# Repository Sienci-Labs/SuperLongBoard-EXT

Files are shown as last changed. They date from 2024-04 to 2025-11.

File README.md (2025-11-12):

# SuperLongBoard-EXT PCB Design
Hardware repo for the SLB-EXT board for the AltMill. These are all the raw build files that we're making available to the public so you can see and access the work that's been put in to make the SuperLongBoard-EXT as it currently exists. If you'd like to make it yourself, modify it, or suggest improvements feel free. Please note and respect the license we've chosen to distribute it under.

# License

This code has been created within the context of Open Hardware and is licensed under the "CERN-OHL-S v2". Please read more about this in the LICENSE file. You could redistribute and modify this source and make products using it under the terms of the CERN-OHL-S v2. This means stuff like licensing your changes reciprocally, giving attribution to us, and releasing hardware that this code runs on as CERN-OHL-S v2 too. Note that this LICENSE applies on all coding work done in prior commits to-date, and is now being released in good faith that no action will be taken to pursue past work in order to duplicate the work we've put in without having to abide by the License that's now being applied at its first public release.

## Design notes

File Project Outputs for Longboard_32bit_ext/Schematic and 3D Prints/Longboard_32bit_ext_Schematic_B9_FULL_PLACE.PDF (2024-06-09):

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
2024-06-09 9:13:34 AM

Title Sheet.SchDoc

SHEET

B

Expatria Technologies

625 Kane Valley Rd.
Box 2084

EMAIL: INFO@EXPATRIA.CA

Copyright Sienci Labs 2024. This document describes Open Hardware
and is licensed under the
CERN-OHL-S v2. No warranty is
implied or expressed. | SIZE

REV

MODIFIED | SHEET
1 27 /

AM

ENGR DOCUMENT

B9

PROJECT
Longboard_32bit_ext.PrjPCB

Merritt, BC V1K1B8

# Mechanical

# Sienci Altmill 32-bit CNC Controller

## Title Sheet

Assembly Note

ZZ1

These assemblies are ESD sensitive, ESD precautions shall be observed.

Assembly Note

ZZ2

These assemblies must be clean and free from flux and all contaminants. Use of no clean flux is not acceptable.

Assembly Note

ZZ3

These assemblies must comply with workmanship standards IPC-A-610 Class 2, unless otherwise specified.

FID1 | FID3 FID2

Sienci CNC Controller
Block_diagram.SchDoc

Sienci CNC Controller
Board_Diagram.SchDoc

D D

C C

B B

A A

2024-06-09 9:13:35 AM

Board_Diagram.SchDoc

SHEET

Expatria Technologies

625 Kane Valley Rd.
Box 2084

Copyright Sienci Labs 2024. This document describes Open Hardware
and is licensed under the
CERN-OHL-S v2. No warranty is
implied or expressed. | SIZE

REV

MODIFIED | SHEET
2 27 /

AM

ENGR DOCUMENT

B9

PROJECT
Longboard_32bit_ext.PrjPCB

Merritt, BC V1K1B8

## Board Diagram

# USBC MCU

# AUX GPIO HEADER Aux Transistor 1

# 72V POWER ENABLE DIRECTION ANALOG GND

# 12V SPIN

# Sienci Altmill 32-bit CNC Controller DOOR

# Ethernet

# MCU SD CARD

# MCU PROGRAM

DEBUG | Aux Relay 1 | Aux Relay 2 | Aux Transistor 2 | AT SPEED | SPIN PWR 12V

# PENDANT

CANBUS | ANALOG_IN | A MOTOR | ALIM

# Ring Light

PROBE | PROBE TLO

# GND

# PWM

# ENABLE LASER

# GND

START BUTTONS | LED POWER

# AUX OUTPUT MATRICES Aux Comms

# Power Toggle

# MACRO1

# MACRO2

# MOT_PWR

# ESTOP

# ESTOP

RS485
RS485
Gantry Light | FLOOD | GND A_LIMIT Z_LIMIT Y2_LIMIT Y1_LIMIT X_LIMIT LIMIT_PWR

# LED

Motor Power | Contactor
Relay Holder A MOTOR | A MOTOR | A MOTOR | A MOTOR

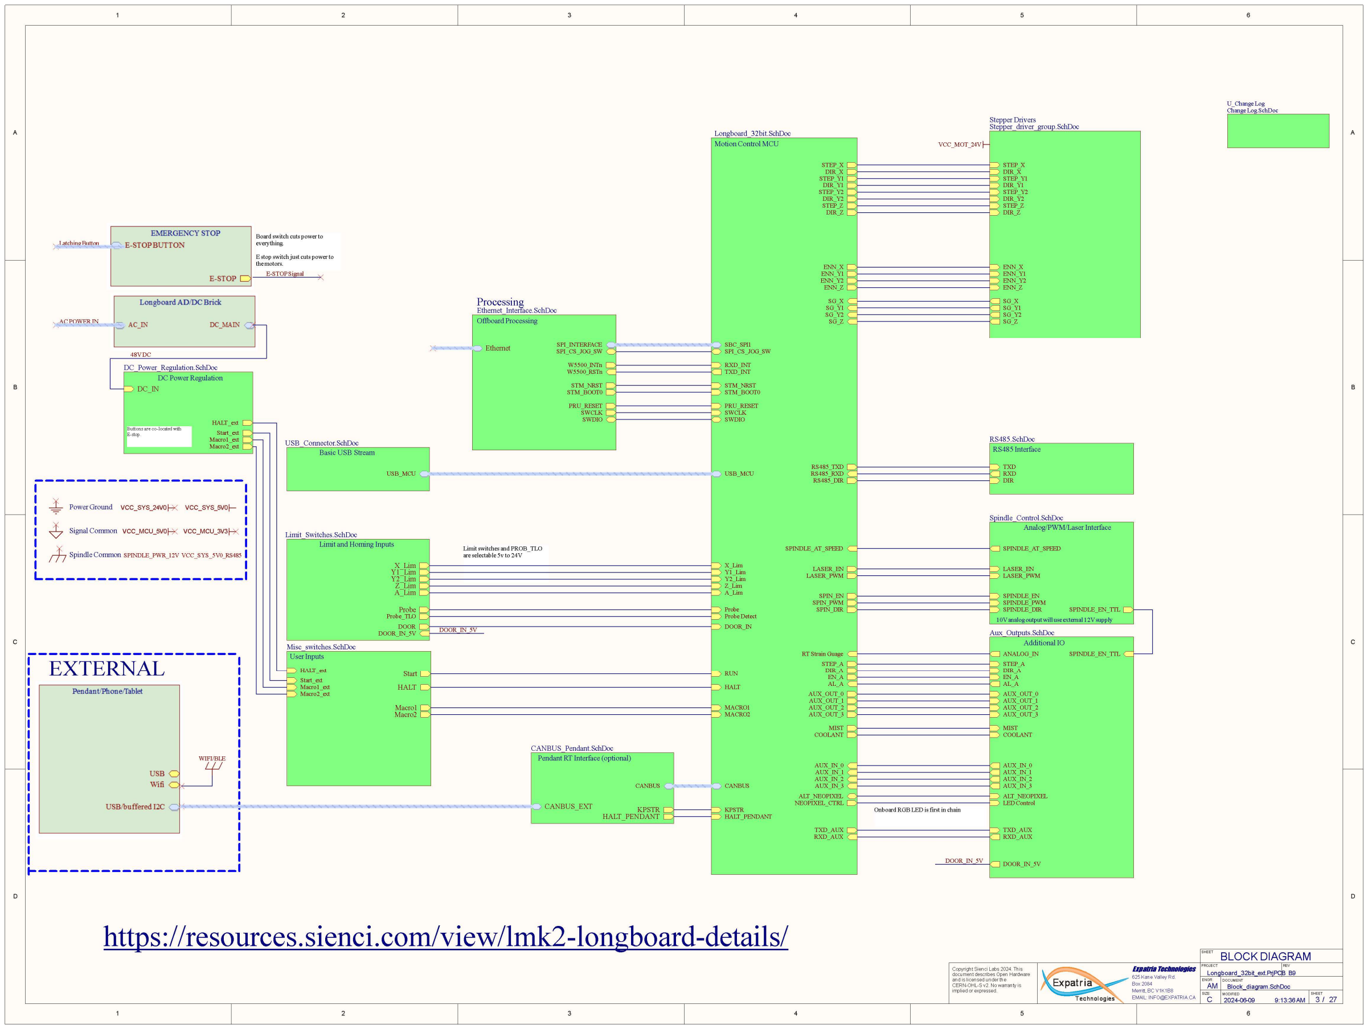
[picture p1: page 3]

D D

C C

B B

A A

2024-06-09 9:13:36 AM

Block_diagram.SchDoc

SHEET

C

Expatria Technologies

SIZE

REV

MODIFIED | SHEET
3 27 /

AM

ENGR DOCUMENT

B9

PROJECT
Longboard_32bit_ext.PrjPCB Copyright Sienci Labs 2024. This document describes Open Hardware
and is licensed under the
CERN-OHL-S v2. No warranty is
implied or expressed.

625 Kane Valley Rd.
Box 2084
Merritt, BC V1K1B8

RS485_TXD

SPIN_PWM

X_Lim
Y1_Lim
Y2_Lim
Z_Lim

SPINDLE_AT_SPEED

RUN

A_Lim | SPIN_EN

Probe

RT Strain Guage

COOLANT

MIST

Probe Detect

STEP_X
DIR_X
STEP_Y1
DIR_Y1

STEP_Z
DIR_Z

STEP_Y2
DIR_Y2

STEP_A
DIR_A

SPIN_DIR

AUX_OUT_0
AUX_OUT_1
AUX_OUT_2
AUX_OUT_3

AUX_IN_0
AUX_IN_1
AUX_IN_2
AUX_IN_3

NEOPIXEL_CTRL
KPSTR

HALT

ENN_X
ENN_Y1

ENN_Z

ENN_Y2

SG_X
SG_Y1

SG_Z

SG_Y2

EN_A
AL_A

SPI_CS_JOG_SW

LASER_PWM

LASER_EN

MACRO1
MACRO2

RS485_RXD
RS485_DIR

SBC_SPI1

STM_NRST
STM_BOOT0

RXD_INT
TXD_INT

CANBUS

RXD_AUX

TXD_AUX

PRU_RESET
SWCLK
SWDIO

HALT_PENDANT

DOOR_IN

ALT_NEOPIXEL

USB_MCU

Motion Control MCU

Longboard_32bit.SchDoc

### BLOCK DIAGRAM

X_Lim
Y1_Lim
Y2_Lim
Z_Lim
A_Lim

Probe
Probe_TLO
DOOR
DOOR_IN_5V

Limit and Homing Inputs

Limit_Switches.SchDoc

HALT

Start

Macro1
Macro2

Start_ext
Macro1_ext

HALT_ext

Macro2_ext

User Inputs

Misc_switches.SchDoc

LASER_PWM

LASER_EN

SPINDLE_PWM

SPINDLE_EN

SPINDLE_DIR

SPINDLE_AT_SPEED

SPINDLE_EN_TTL

Analog/PWM/Laser Interface

Spindle_Control.SchDoc

DIR

RXD

TXD

RS485 Interface

RS485.SchDoc

SPI_INTERFACE Ethernet | SPI_CS_JOG_SW

STM_NRST
STM_BOOT0

SWCLK
SWDIO

PRU_RESET

W5500_INTn
W5500_RSTn

Offboard Processing

Ethernet_Interface.SchDoc
AC POWER IN

DC_IN

Start_ext
Macro1_ext
Macro2_ext

HALT_ext

DC Power Regulation

DC_Power_Regulation.SchDoc

48V DC

Latching Button

STEP_X
DIR_X
STEP_Y1
DIR_Y1

STEP_Z
DIR_Z

STEP_Y2
DIR_Y2

ENN_X
ENN_Y1

ENN_Z

ENN_Y2

SG_X
SG_Y1

SG_Z

SG_Y2

Stepper Drivers
Stepper_driver_group.SchDoc

VCC_MOT_24V

### Processing

10V analog output will use external 12V supply

Onboard RGB LED is first in chain

STEP_A
DIR_A

AUX_OUT_0
AUX_OUT_1
AUX_OUT_2
AUX_OUT_3

AUX_IN_0
AUX_IN_1
AUX_IN_2
AUX_IN_3

LED Control

EN_A
AL_A

RXD_AUX

TXD_AUX

ANALOG_IN

COOLANT

MIST

SPINDLE_EN_TTL

ALT_NEOPIXEL

DOOR_IN_5V

Additional IO

Aux_Outputs.SchDoc

WIFI/BLE

CANBUS_EXT | KPSTR HALT_PENDANT CANBUS

Pendant RT Interface (optional)

CANBUS_Pendant.SchDoc

E-STOP Signal

Board switch cuts power to everything.

E stop switch just cuts power to the motors.

# https://resources.sienci.com/view/lmk2-longboard-details/

U_Change Log
Change Log.SchDoc

USB_MCU

Basic USB Stream

USB_Connector.SchDoc

Limit switches and PROB_TLO are selectable 5v to 24V

Buttons are co-located with E-stop.

# EXTERNAL

VCC_MCU_5V0 VCC_MCU_3V3

VCC_SYS_24V0

Spindle Common

Signal Common

Power Ground | VCC_SYS_5V0

SPINDLE_PWR_12V VCC_SYS_5V0_RS485

DOOR_IN_5V

DOOR_IN_5V

D D

C C

B B

A A

2024-06-09 9:13:36 AM

Longboard_32bit.SchDoc

SHEET

Expatria Technologies

625 Kane Valley Rd.
Box 2084

Copyright Sienci Labs 2024. This document describes Open Hardware
and is licensed under the
CERN-OHL-S v2. No warranty is
implied or expressed. | SIZE

REV

MODIFIED | SHEET
4 27 /

AM

ENGR DOCUMENT

B9

PROJECT
Longboard_32bit_ext.PrjPCB

Merritt, BC V1K1B8

## Sienci Longboard EXT

USB_D_P

DIR_A

RXD_INT

DIR_Y1

USB_D_N

DIR_X

STEP_A

TXD_INT

STEP_Y2

SPI1_CK

STEP_Z

STEP_Y1

SPI1_MISO

SPI1_MOSI

SPIN_SPEED

STEP_X

CYC/ST

SPI1_CS_JOG_SW

PROBE

AUXOUT3

TXD_EXT

SDA

AUXOUT2

AUXOUT0

Y2_LIM

SCL

DIR_Z

KPSTR

RXD_EXT

HALT

AUXOUT1

DIR_Y2

PRU_RESET

X_LIM

Z_LIM

STM_BOOT0

Y1_LIM

STEP_EN_X

A_LIM

STM_RESET

STEP_EN_Y1

LASER_PWM

LASER_EN

SPINDLE_PWM
SPINDLE_DIR

SPINDLE_EN

STEP_EN_Z
STEP_EN_Y2
STEP_EN_A

SG_Y2

SG_Z

SG_Y1

SG_X

AL_A

MIST
COOLANT

AUX_IN_0

MACRO1
MACRO2

AUX_IN_1
AUX_IN_2
AUX_IN_3

PROBE_DET

RS485_DIR

NEO_LED

RT Strain Guage

CAN_TX
CAN_RX

SWCLK

SWDIO

RXD_AUX

TXD_AUX

DOOR

ALT_NEOPIXEL

Microcontroller
MCU_STM32F412VGT6.SchDoc

SPI_CS_JOG_SW

SBC_SPI_PICO
SBC_SPI_POCI

SBC_SPI_CLK

SCL
SDA
KPSTR
TXD_INT
RXD_INT

TXD_EXT
RXD_EXT

AUXOUT_1
AUXOUT_2
AUXOUT_3

CYC/ST

PROBE

PRU_RESET

HALT_n

STM_BOOT0
STM_RESET

DIR_Y1

SPI_CS_JOG_SW

ENN_X

MACRO1

STEP_A

STM_NRST

NEOPIXEL_CTRL

SG_Y1

STEP_Y2

DIR_Y2
DIR_A

USB_MCU

KPSTR

RS485_RXD

Probe

SPIN_PWM

SG_X

AUX_OUT_3

SG_Z

LASER_PWM

SPIN_EN

AUX_IN_1

DIR_X

RS485_DIR

AUX_IN_0

RS485_TXD

AUX_IN_2

Z_Lim

RT Strain Guage

ENN_Y1

AUX_OUT_2

MACRO2

AUX_OUT_0
AUX_OUT_1

Y1_Lim

STM_BOOT0

ENN_Z

Probe Detect

STEP_X

EN_A

AUX_IN_3

ENN_Y2

DIR_Z

X_Lim

RUN

SPIN_DIR

STEP_Z

SPI_CLK
SPI_PICO
SPI_POCI

SPI

VCC_MCU_3V3
R8
10KΩ ±1%

C1
100nF

HALT_n

STEP_Y1

SPINDLE_EN
SPINDLE_PWM
SPINDLE_DIR

SG_Y2
AL_A

MIST COOLANT

MIST
COOLANT

LASER_EN

RXD_INT

TXD_INT

SBC_SPI1

USB_D_P
USB_D_N

USB2

CANBUS | CAN_TX CAN_RX

CANBUS

RXD_AUX

TXD_AUX

PRU_RESET

SWDIO
SWCLK

HALT_PENDANT

HALT

1

2

4

U1A

SN74AHC1G86DBVR

GND 3 VCC 5

U1B

SN74AHC1G86DBVR

C2
100nF

VCC_MCU_3V3

SPINDLE_AT_SPEED

Y2_Lim
A_Lim

TP3
TP4
TP5
TP6

SPI_CS_JOG_SW

SBC_SPI_PICO
SBC_SPI_POCI

SBC_SPI_CLK

TP11
TP13

TP18

TP20 | TP19

TP22
TP23
TP24
TP26
TP28
TP16 | TP17
TP7 | TP9

TP14

TP15

TP31
TP32

TP37
TP38 | TP36

TP21

DOOR_IN

ALT_NEOPIXEL | Shared with SWDIO

TP1
TP2
TP33
TP34

TP53
TP54
TP55
TP56
TP58 | TP57
TP59

TP61

TP35
TP39
TP40
TP41
TP42

TP43
TP44
TP45
TP46
TP47
TP48
TP49
TP50
TP51
TP52

TP60

AUXOUT_0

These are used for Ethernet signals

AUXOUT1 | MIST SPINDLE_DIR Y¹_LIM | X_LIM

# SD_CSn AL_A

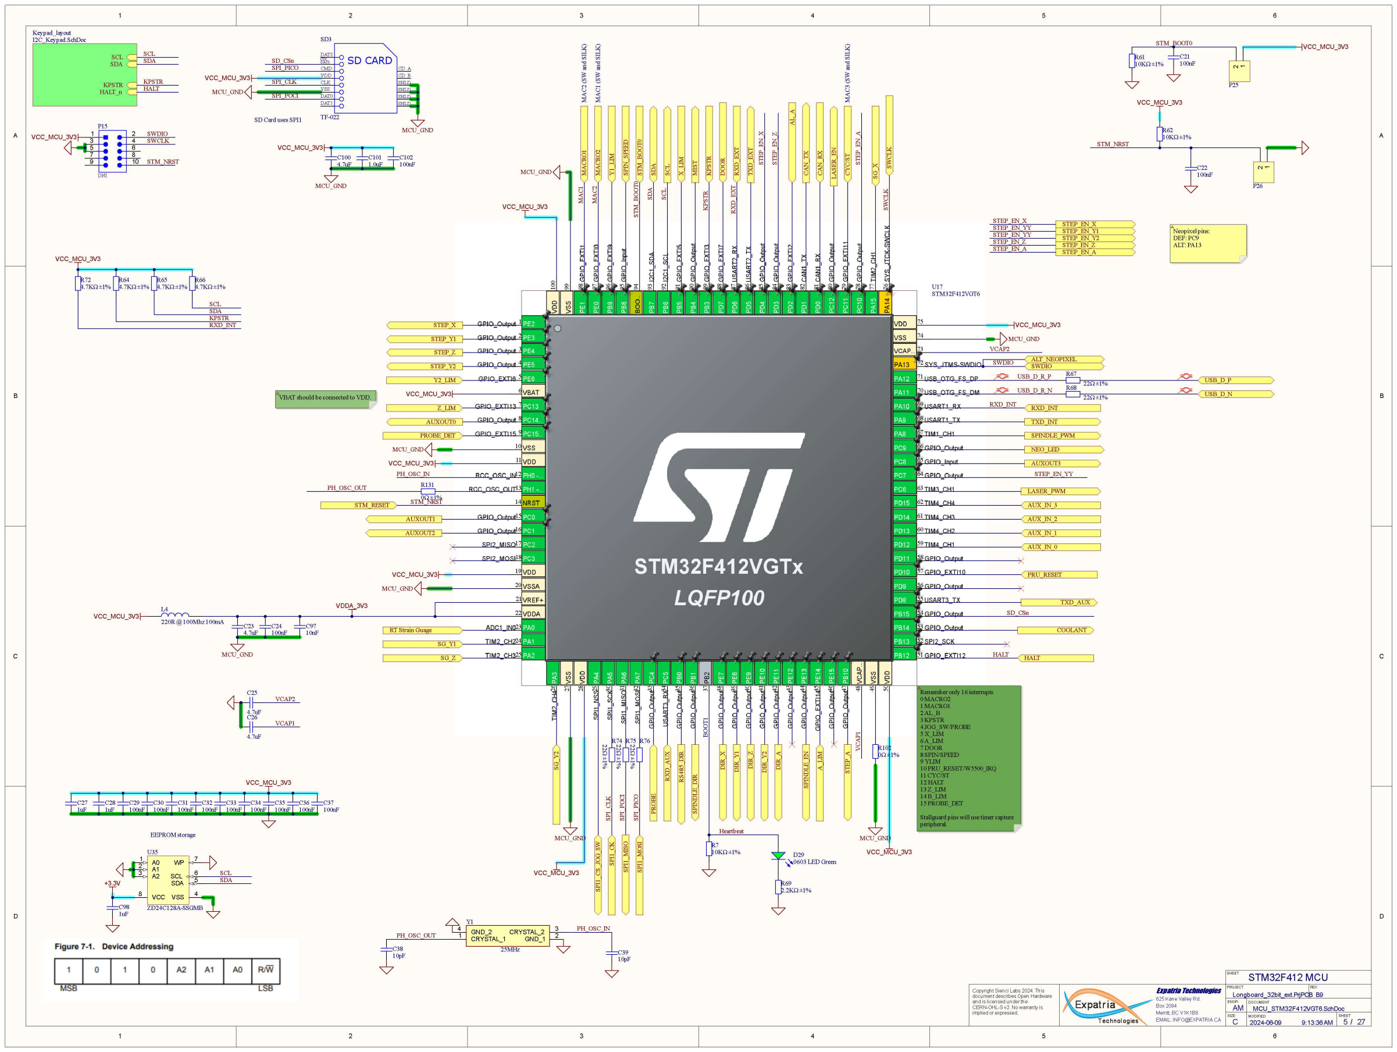
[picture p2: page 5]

D D

C C

B B

A A

2024-06-09 9:13:36 AM

MCU_STM32F412VGT6.SchDoc

SHEET

C

Expatria Technologies

SIZE

REV

MODIFIED | SHEET
5 27 /

AM

ENGR DOCUMENT

B9

PROJECT
Longboard_32bit_ext.PrjPCB Copyright Sienci Labs 2024. This document describes Open Hardware
and is licensed under the
CERN-OHL-S v2. No warranty is
implied or expressed.

625 Kane Valley Rd.
Box 2084

Merritt, BC V1K1B8 ⁸⁹

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
25 | 26 | 27 | 28 | 29 | 30 | 31 | 32 | 33 | 34 | 35 | 36 | 37 | 38 | 39 | 40 | 41 | 42 | 43 | 44 | 45 | 46 | 47 | 48 | 49 | 50

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
51 ¹⁰⁰ 99 | 98 | 97 | 96 | 95 | 94 | 93 | 92 | 91 | 90 | 88 | 87 | 86 | 85 | 84 | 83 | 82 | 81 | 80 | 79 | 78 | 77 | 76 | U17
STM32F412VGT6

STM_NRST

R61
10KΩ ±1%

C21
100nF

VCC_MCU_3V3

R62
10KΩ ±1%

VCC_MCU_3V3

CRYSTAL_1 1 | GND_1 | 2
CRYSTAL_2 | 3 GND_2 4

25MHz

Y1

C39
10pF

C38
10pF

PH_OSC_IN
PH_OSC_OUT

C29
100nF

C30
100nF

C31
100nF

C32
100nF

C33
100nF

C34
100nF

C35
100nF

VCC_MCU_3V3

C28
1uF

R66
4.7KΩ ±1%

R65
4.7KΩ ±1%

VCC_MCU_3V3

SCL
SDA

STM32F412 MCU

C22
100nF

KPSTR

R64
4.7KΩ ±1%

C26

4.7uF

C25

4.7uF

3

1
4

2

5 6
7 8
9 10

P15

DNI

STM_NRST

SWDIO
SWCLK VCC_MCU_3V3

PH_OSC_IN

PH_OSC_OUT

Z_LIM | A_LIM | CYC/ST

R67
22Ω ±1% R68
22Ω ±1% | USB_D_N

USB_D_P BOOT¹

HALT

SPINDLE_PWM

USB_D_R_N

USB_D_R_P SPINDLE_EN

AUXOUT0

STM_NRST | STM_BOOT⁰ STM_BOOT⁰

VCAP2

VCAP2

VCC_MCU_3V3

VCC_MCU_3V3

MCU_GND

MCU_GND

MCU_GND

MCU_GND

VCC_MCU_3V3

VCC_MCU_3V3 | SG_Y²

LASER_PWM LASER_EN

SG_Y1

AUX_IN_1 MACRO¹ | CAN_TX | CAN_RX

NEO_LED MACRO² SPI1_CS_JOG_SW

RT Strain Guage | SWCLK

STEP_Z

STEP_Y2 | DIR_X

STEP_X

STEP_Y1 | DIR_Y¹ | DIR_Z | DIR_Y² | DIR_A RXD_EXT | TXD_EXT

VCC_MCU_3V3

MCU_GND

SG_Z | SG_X

AUX_IN_2

AUX_IN_0

AUX_IN_3

VCC_MCU_3V3

# MCU_GND VCAP¹

PROBE_DET

AUXOUT2

STM_RESET

C27
1uF

C36
100nF

C37
100nF

L4
220R @ 100Mhz 100mA C23
4.7uF

C24
100nF

MCU_GND

VDDA_3V3

VCC_MCU_3V3 | SPI1_CK | SPI1_MISO | SPI1_MOSI 22Ω ±1%

R7422Ω ±1%

R7522Ω ±1%

R76

SWDIO

SCL
SDA

KPSTR
HALT_n

Keypad_layout
I2C_Keypad.SchDoc

HALT

KPSTR
HALT

SDA

SCL | RS⁴⁸⁵_DIR

TXD_INT

RXD_INT

TXD_AUX RXD_AUX

STEP_EN_Z

STEP_EN_X
STEP_EN_Y1
STEP_EN_Y2
STEP_EN_A STEP_EN_X | STEP_EN_Z | STEP_EN_A

STEP_EN_A

STEP_EN_Z

STEP_EN_YY

STEP_EN_YY
STEP_EN_YY

STEP_EN_X SWCLK

SWDIO SPIN_SPEED

A0 1

SDA 5

A2 3

A1 2 | WP | 7
VSS | 4
SCL | 6

VCC 8

U35

ZD24C128A-SSGMB

+3.3V

C98
1uF

SCL
SDA

EEPROM storage

C97
10nF

R131
0Ω ±1%

R7
10KΩ ±1%

C102
100nF

C100
4.7uF

C101
1.0uF

VCC_MCU_3V3

DAT3
CMD
VDD
CLK
VSS
DAT0
DAT1

DAT2
CD/ SD CARD

CD_A
CD_B
SHLD
SHLD

SHLD

SHLD

SD3

TF-022

VCC_MCU_3V3 SPI_CLK SPI_PICO

SPI_POCI

SD_CSn

RXD_INT

RXD_INT | RXD_EXT

R72

4.7KΩ ±1% | SPI_CLK | SPI_POCI | SPI_PICO

SD Card uses SPI1

VCC_MCU_3V3 | SDA SDA | SCL SCL
Y2_LIM | STEP_A DOOR

COOLANT

D29
0603 LED Green

R69
2.2KΩ ±1%

Heartbeat

ALT_NEOPIXEL

MCU_GND

MCU_GND

MCU_GND | MAC¹ | MAC²

STM_BOOT0 PROBE

AUXOUT3

R102
0Ω ±1%

P25 2

1

P26

VCAP1 | KPSTR KPSTR
PRU_RESET MAC² ⁽SW and SILK⁾ | MAC¹ ⁽SW and SILK⁾ | MAC³ ⁽SW and SILK⁾

Remember only 16 interrupts

### 0 MACRO2 1 MACRO1 2 AL_B 3 KPSTR 4 JOG_SW/PROBE 5 X_LIM 6 A_LIM 7 DOOR 8 SPIN/SPEED 9 YLIM 10 PRU_RESET/W5500_IRQ 11 CYC/ST 12 HALT 13 Z_LIM 14 B_LIM 15 PROBE_DET

Stallguard pins will use timer capture peripheral.

VBAT should be connected to VDD.

Neopixel pins:
DEF: PC9
ALT: PA13

D D

C C

B B

A A

2024-06-09 9:13:37 AM

I2C_Keypad.SchDoc

SHEET

Expatria Technologies

625 Kane Valley Rd.
Box 2084

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

REV

MODIFIED | SHEET
6 27 /

AM

ENGR DOCUMENT

B9

PROJECT
Longboard_32bit_ext.PrjPCB

Merritt, BC V1K1B8

## Misc Switches

VCC_MCU_3V3

SCL
SDA

VCC_MCU_5V0

HALT_n
KPSTR

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
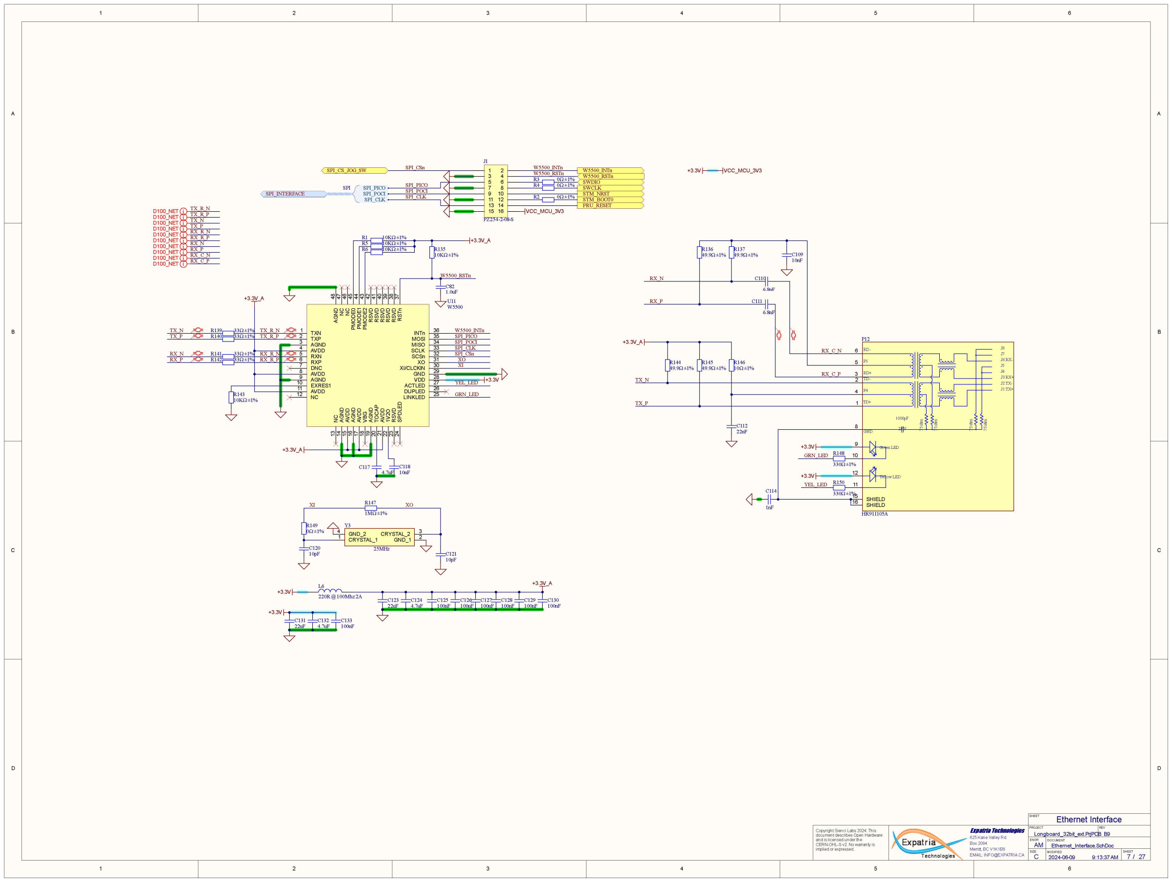
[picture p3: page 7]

D D

C C

B B

A A

Ethernet_Interface.SchDoc

SHEET

C

Expatria Technologies

SIZE

REV

MODIFIED | SHEET
7 27 /

AM

ENGR DOCUMENT

B9

PROJECT
Longboard_32bit_ext.PrjPCB Copyright Sienci Labs 2024. This document describes Open Hardware
and is licensed under the
CERN-OHL-S v2. No warranty is
implied or expressed.

625 Kane Valley Rd.
Box 2084
Merritt, BC V1K1B8

Ethernet Interface

STM_BOOT0

SPI_INTERFACE | STM_NRST

SPI_CS_JOG_SW

| SWCLK

SWDIO

SPI_CLK

SPI_PICO
SPI_POCI

SPI
R2 | 0Ω ±1%
R3 | 0Ω ±1%
R4 | 0Ω ±1%

1 2
3 4
5 6
7 8
9 10
11 12
13 14
15 16

J1

PZ254-2-08-S

W5500_RSTn

W5500_INTn

PRU_RESET
VCC_MCU_3V3

TXP 2
AGND 3
AVDD 4
RXN 5
RXP 6
DNC 7
AVDD 8

EXRES1 10
AVDD 11
NC 12 | NC 13 AGND 14 AVDD 15 AGND 16 AVDD 17 VBG 18 AGND 19 TOCAP 20 AVDD 21 1V²O 22 RSVD 23 SPDLED 24
LINKLED | 25 DUPLED | 26 ACTLED | 27 VDD | 28 GND | 29 XI/CLCKIN | 30 XO | 31 SCSn | 32 SCLK | 33 MISO | 34 MOSI | 35 INTn | 36 RSTn 37 RSVD ³⁸ RSVD ³⁹ RSVD ⁴⁰ RSVD ⁴¹ RSVD ⁴² PMODE² ⁴³ PMODE¹ ⁴⁴ PMODE⁰ ⁴⁵ NC ⁴⁶ NC ⁴⁷ AGND ⁴⁸

TXN 1

AGND 9

U11
W5500
R1 | 10KΩ ±1%
R5 | 10KΩ ±1%
R6 | 10KΩ ±1%

L6
220R @ 100Mhz 2A | C123 22uF
C124
4.7uF

+3.3V

+3.3V_A

CRYSTAL_1 1 | GND_1 | 2
CRYSTAL_2 | 3 GND_2 4

25MHz

Y3

C121
10pF

C120
10pF

R149
0Ω ±1%

R147
1MΩ ±1%
XI | XO

+3.3V

C125
100nF

C126
100nF

C127
100nF

C128
100nF

C129
100nF

C130
100nF

C131
22uF

C132
4.7uF

C133
100nF

C117
4.7uF

+3.3V_A

C118
10nF

GRN_LED

YEL_LED +3.3V

XI

XO

SPI_PICO
SPI_POCI
SPI_CLK
R139 | 33Ω ±1% | W5500_INTn
R140 | 33Ω ±1%
R141 | 33Ω ±1%
R142 | 33Ω ±1%

TX_R_N
TX_R_P

RX_R_N
RX_R_P

TX_N
TX_P

RX_N
RX_P

+3.3V_A

R143
10KΩ ±1%

W5500_RSTn

R135
10KΩ ±1%

SPI_CSn

+3.3V_A

C82
1.0uF

SPI_PICO
SPI_POCI
SPI_CLK
SPI_CSn | W5500_INTn W5500_RSTn

D100_NET i

TX_N
TX_P

RX_N
RX_P

TX_R_N
TX_R_P

RX_R_N
RX_R_P

RX_C_N
RX_C_P D100_NET i

D100_NET i

D100_NET i

D100_NET i

D100_NET i

D100_NET i

D100_NET i

D100_NET i

D100_NET i

+3.3V | VCC_MCU_3V3

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
SHIELD 15
SHIELD 16

J8
J7
J6 RX-J5
J4
J3 RX+
J2 TX-J1 TX+

Yellow LED

Green LED | 75ohm | 75ohm | 75ohm | 75ohm1000pF

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
HR911105A

GRN_LED

YEL_LED
C114

1nF

+3.3V

+3.3V

R148

330Ω ±1%

R150

330Ω ±1%

RX_N

RX_P

R136
49.9Ω ±1%

R146
10Ω ±1%

C110

6.8nF

C109
10nF

C112
22nF

R145
49.9Ω ±1%

R144
49.9Ω ±1%

TX_N

TX_P

+3.3V_A

C111

6.8nF

R137
49.9Ω ±1%

RX_C_N

RX_C_P

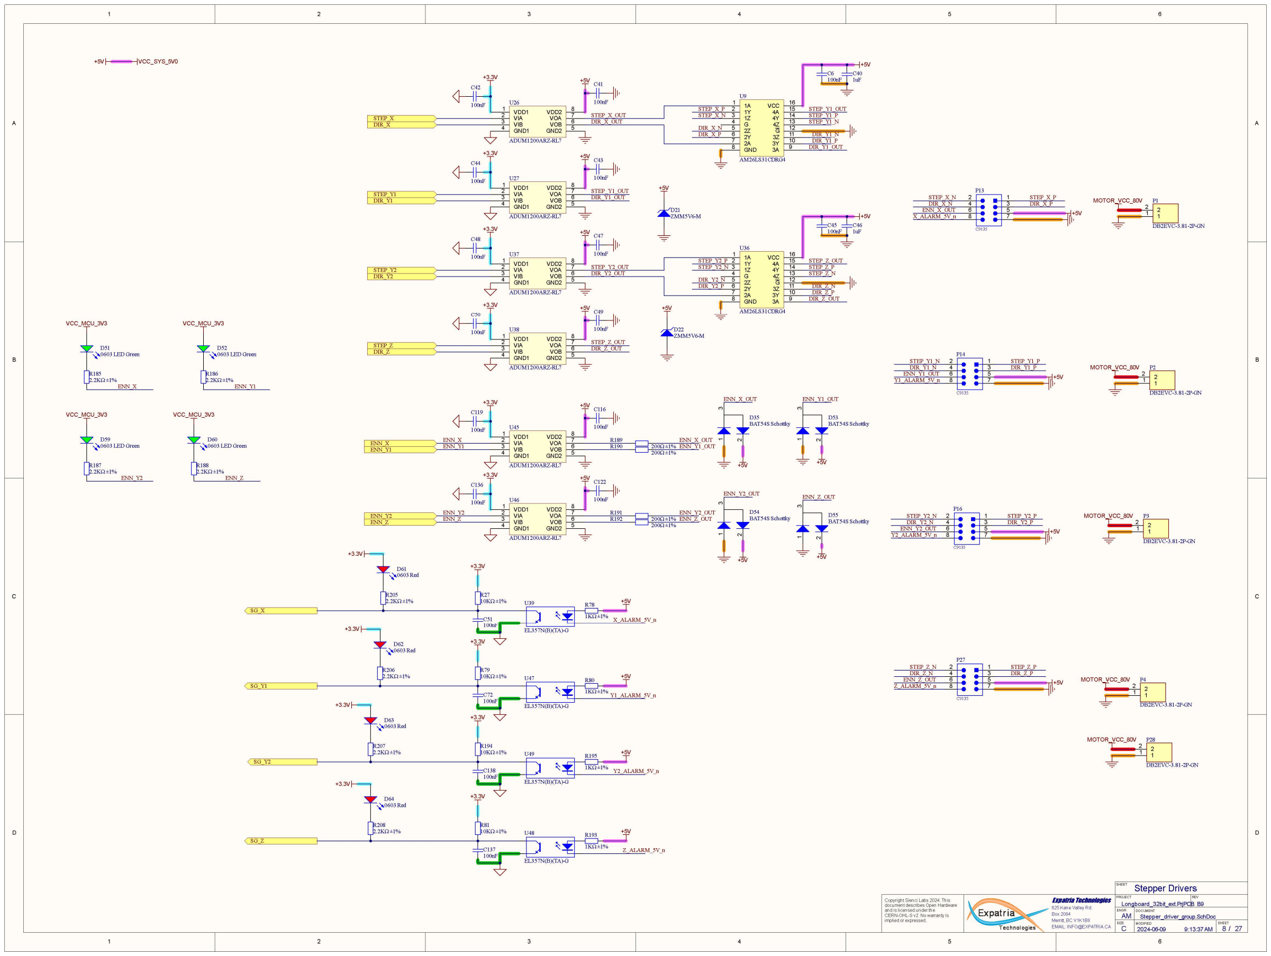
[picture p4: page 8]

D D

C C

B B

A A

Stepper_driver_group.SchDoc

SHEET

C

Expatria Technologies

SIZE

REV

MODIFIED | SHEET
8 27 /

AM

ENGR DOCUMENT

B9

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

625 Kane Valley Rd.
Box 2084
Merritt, BC V1K1B8

Stepper Drivers

SG_X

ENN_X
ENN_Y1

SG_Y1

SG_Z

ENN_Z

SG_Y2

ENN_Y2

1A 1
1Y 2
1Z 3
G

4
2Z 5
2Y 6
2A 7
GND 8
3A | 9
3Y | 10 3Z | 11 G
12 4Z | 13 4Y | 14 4A | 15 VCC | 16

U9

AM26LS31CDRG4

STEP_X_N

STEP_X_P

+5V

VDD1 1
| VOA | 7
VIB 3
GND1 4 | GND2 | 5
| VOB | 6

VIA 2

VDD2 8

U26

ADUM1200ARZ-RL7

+5V +3.3V

STEP_X_OUT
DIR_X_OUT

C42

100nF

C41

100nF

C6
100nF

C40
1uF

STEP_X
DIR_X | STEP_Y1_N

STEP_Y1_P

DIR_Y1_P

DIR_X_P | DIR_Y1_N

DIR_X_N

VDD1 1
| VOA | 7
VIB 3
GND1 4 | GND2 | 5
| VOB | 6

VIA 2

VDD2 8

U27

ADUM1200ARZ-RL7

+5V +3.3V

STEP_Y1_OUT
DIR_Y1_OUT

C44

100nF

C43

100nF

STEP_Y1_OUT

DIR_Y1_OUT

1A 1
1Y 2
1Z 3
G

4
2Z 5
2Y 6
2A 7
GND 8
3A | 9
3Y | 10 3Z | 11 G
12 4Z | 13 4Y | 14 4A | 15 VCC | 16

U36

AM26LS31CDRG4

STEP_Y2_N

STEP_Y2_P

+5V

VDD1 1
| VOA | 7
VIB 3
GND1 4 | GND2 | 5
| VOB | 6

VIA 2

VDD2 8

U37

ADUM1200ARZ-RL7

+5V +3.3V

STEP_Y2_OUT
DIR_Y2_OUT

C48

100nF

C47

100nF

C45
100nF

C46
1uF

STEP_Z_N

STEP_Z_P

DIR_Z_P

DIR_Y2_P | DIR_Z_N

DIR_Y2_N

VDD1 1
| VOA | 7
VIB 3
GND1 4 | GND2 | 5
| VOB | 6

VIA 2

VDD2 8

U38

ADUM1200ARZ-RL7

+5V +3.3V

STEP_Z_OUT
DIR_Z_OUT

C50

100nF

C49

100nF

STEP_Z_OUT

DIR_Z_OUT

STEP_Y2
DIR_Y2

STEP_Z
DIR_Z

STEP_Y1
DIR_Y1
D21
ZMM5V6-M

+5V

D22
ZMM5V6-M

+5V

VDD1 1
| VOA | 7
VIB 3
GND1 4 | GND2 | 5
| VOB | 6

VIA 2

VDD2 8

U45

ADUM1200ARZ-RL7

+5V +3.3V
C119

100nF

C116

100nF

VDD1 1
| VOA | 7
VIB 3
GND1 4 | GND2 | 5
| VOB | 6

VIA 2

VDD2 8

U46

ADUM1200ARZ-RL7

+5V +3.3V
C136

100nF

C122

100nF

ENN_X_OUT
ENN_Y1_OUT

ENN_Y2_OUT
ENN_Z_OUT

R189
R190 | 200Ω ±1%
| 200Ω ±1%

R191
R192 | 200Ω ±1%
| 200Ω ±1%

Z_ALARM_5V_n

Y2_ALARM_5V_n

Y1_ALARM_5V_n

X_ALARM_5V_n

U39

EL357N(B)(TA)-G

R78
1KΩ ±1%

+5V

R27
10KΩ ±1%

+3.3V

C51
100nF

U47

EL357N(B)(TA)-G

R80
1KΩ ±1%

+5V

R79
10KΩ ±1%

+3.3V

C72
100nF

U49

EL357N(B)(TA)-G

R195
1KΩ ±1%

+5V

R194
10KΩ ±1%

+3.3V

C138
100nF

U48

EL357N(B)(TA)-G

R193
1KΩ ±1%

+5V

R81
10KΩ ±1%

+3.3V

C137
100nF

STEP_X_N
DIR_X_N

STEP_X_P
DIR_X_P
ENN_X_OUT
X_ALARM_5V_n | 1

1

| 2

2

P1

DB2EVC-3.81-2P-GN

MOTOR_VCC_80V

1

1

2

2

P2

DB2EVC-3.81-2P-GN

MOTOR_VCC_80V

1

1

2

2

P3

DB2EVC-3.81-2P-GN

MOTOR_VCC_80V

1

1

2

2

P4

DB2EVC-3.81-2P-GN

MOTOR_VCC_80V ¹ ³ 2
D35

BAT54S Schottky 1 3 2
D53
BAT54S Schottky 1 3 2

D54

BAT54S Schottky 1 3 2
D55
BAT54S Schottky
+5V | +5V

+5V +5V

ENN_X_OUT | ENN_Y1_OUT
ENN_Y2_OUT | ENN_Z_OUT

D51
0603 LED Green

R185
2.2KΩ ±1%

VCC_MCU_3V3

3

1
4

2

6 5
8 7

P13

C9135

+5V

STEP_Y1_N
DIR_Y1_N

STEP_Y1_P
DIR_Y1_P
ENN_Y1_OUT
Y1_ALARM_5V_n

3

1
4

2

6 5
8 7

P14

C9135

+5V

STEP_Y2_N
DIR_Y2_N

STEP_Y2_P
DIR_Y2_P
ENN_Y2_OUT
Y2_ALARM_5V_n

3

1
4

2

6 5
8 7

P16

C9135

+5V

STEP_Z_N
DIR_Z_N

STEP_Z_P
DIR_Z_P
ENN_Z_OUT
Z_ALARM_5V_n

3

1
4

2

6 5
8 7

P27

C9135

+5V

D61
0603 Red

R205
2.2KΩ ±1%

+3.3V

D62
0603 Red

R206
2.2KΩ ±1%

+3.3V

D63
0603 Red

R207
2.2KΩ ±1%

+3.3V

D64
0603 Red

R208
2.2KΩ ±1%

+3.3V

ENN_X
ENN_Y1

ENN_Y2
ENN_Z

ENN_X

D52
0603 LED Green

R186
2.2KΩ ±1%

VCC_MCU_3V3

ENN_Y1

D59
0603 LED Green

R187
2.2KΩ ±1%

VCC_MCU_3V3

ENN_Y2

D60
0603 LED Green

R188
2.2KΩ ±1%

VCC_MCU_3V3

ENN_Z

1

1

2

2

P28

DB2EVC-3.81-2P-GN

MOTOR_VCC_80V

+5V | VCC_SYS_5V0

D D

C C

B B

A A

Aux_Outputs.SchDoc

SHEET

Expatria Technologies

625 Kane Valley Rd.
Box 2084

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

REV

MODIFIED | SHEET
9 27 /

AM

ENGR DOCUMENT

B9

PROJECT
Longboard_32bit_ext.PrjPCB

Merritt, BC V1K1B8

## Auxilliary IO

AL_A

AUX_IN_1

AUX_OUT_3

AUX_IN_3

DIR_A

AUX_OUT_0

EN_A

AUX_IN_2

AUX_OUT_2

AUX_OUT_1

STEP_A

LED Control

AUX_IN_0

ANALOG_IN

RELAY_DRIVE

RL1
Relay_Driver.SchDoc

RELAY_DRIVE

RL2
Relay_Driver.SchDoc

MIST

COOLANT

LED_CONTROL | LED_CONTROL_OUT
RING_LED_CTRL | RING_LED_OUT

LED
Neopixel_Driver.SchDoc

TRN_DRIVE

TR1
Transistor_Driver.SchDoc

STEP_A

EN_A
AL_A_n

DIR_A
EN_A_EXT

DIR_A_EXT

STP_ALARM_5V_n

STEP_A_EXT

MOT
External_Stepper.SchDoc

SPINDLE_EN_TTL

3V_INPUT | 5V_OUT
5V_Digital_Out.SchDoc | AO0
3V_INPUT | 5V_OUT
5V_Digital_Out.SchDoc | AO1
3V_INPUT | 5V_OUT
5V_Digital_Out.SchDoc | AO2
3V_INPUT | 5V_OUT
5V_Digital_Out.SchDoc | AO3
3V_INPUT | 5V_OUT
5V_Digital_Out.SchDoc | COO
3V_INPUT | 5V_OUT
5V_Digital_Out.SchDoc | MIS

AUX_OUT_0_5V

AUX_OUT_1_5V

AUX_OUT_2_5V

AUX_OUT_3_5V

COOLANT_5V

MIST_5V

SPINDLE_EN_5V

AUX_OUT_0_5V

AUX_OUT_1_5V

AUX_OUT_2_5V

AUX_OUT_3_5V

1 2

5 6

3 4

7 8
9 10
11 12
13 14
15 16
17 18
19 20
21 22
23 24
25 26
27 28
29 30
31 32
33 34
35 36
37 38
39 40

P11

321040SG0ABK00A01

1

1

2

2

J13

DB2EVC-3.81-2P-GN

R60
2.2KΩ ±1% | R58
| 5.1KΩ ±1%
R59 | 510Ω ±1%
| C20 8.2nF

Analog Input

RXD_AUX
TXD_AUX | AUX_TXD_5V

AUX_RXD_5V

3V3_OUT | 5V_INPUT
3V3_Digital_Out.SchDoc | N0
3V3_OUT | 5V_INPUT
3V3_Digital_Out.SchDoc | N1
3V3_OUT | 5V_INPUT
3V3_Digital_Out.SchDoc | N2
3V3_OUT | 5V_INPUT
3V3_Digital_Out.SchDoc | N3

AUX_IN0_5V

AUX_IN1_5V

AUX_IN2_5V

AUX_IN3_5V

TRN_DRIVE

TR2
Transistor_Driver.SchDoc

VCC_SYS_24V0

VCC_SYS_5V0

AUX_IN1_5V

AUX_IN2_5V

AUX_IN3_5V

AUX_TXD_5V
AUX_RXD_5V

AUX_OUT_0_5V
AUX_OUT_1_5V

AUX_OUT_2_5V
AUX_OUT_3_5V

COOLANT_5V
MIST_5V

AUX_IN0_5V

SPINDLE_EN_5V

STEP_A_EXT
DIR_A_EXT
EN_A_EXT
STP_ALARM_5V_n

STEP_A_EXT

DIR_A_EXT
EN_A_EXT
STP_ALARM_5V_n

LED_CONTROL_OUT

2

1

J34

WJ15EDGK-3.81-2P

D34
0603 LED Blue
1 3 2

Q7
2N7002-7-F

R156
4.7KΩ ±1%

VCC_MCU_5V0

R158
10KΩ ±1%

D33
0603 LED Blue
1 3 2

Q6
2N7002-7-F

R155
4.7KΩ ±1%

VCC_MCU_5V0

R157
10KΩ ±1%

DOOR_IN_5V

COOLANT

MIST

COOLANT | MIST
ALT_NEOPIXEL | RING_LED_OUT

VCC_SYS_5V0

2

1

J16

WJ15EDGK-3.81-2P

1

1

2

2

J17

DB2EVC-3.81-2P-GN

VDD1 1
| VIA | 7
VIB 3
GND1 4 | GND2 | 5
| VOB | 6

VOA 2

VDD2 8

U20

CBMuD1201LAS8

C71

100nF

C70

100nF | R112 200Ω ±1%
R110
200Ω ±1%

VCC_MCU_3V3

VCC_SYS_5V0

ADC_INPUT

ADC_INPUT

Note that this requires external isolation/protection.

D D

C C

B B

A A

Relay_Driver.SchDoc

SHEET

Expatria Technologies

625 Kane Valley Rd.
Box 2084

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

REV

MODIFIED | SHEET
10 27 /

AM

ENGR DOCUMENT

B9

PROJECT
Longboard_32bit_ext.PrjPCB

Merritt, BC V1K1B8

RELAY_DRIVE

D30 ⁽D30_RL1, ...)
B5819W SL

Q2 ⁽Q2_RL1, ...)
ST3422A

AUX0_RLY

R109 ⁽R109_RL1, ...)
1KΩ ±1%

1

1

2

2

P18 ⁽P18_RL1, ...)

DB2EVC-3.81-2P-GN

## Relay Driver

2

1

J31 ⁽J31_RL1, ...)

WJ15EDGK-3.81-2P

VCC_SYS_24V0

D43⁽D43_RL1, ...)
0603 LED Green

R105 ⁽R105_RL1, ...)
4.7KΩ ±1%

VCC_SYS_5V0

R89 ⁽R89_RL1, ...)
10KΩ ±1%

1 3 2

Q10 ⁽Q10_RL1, ...)
2N7002-7-F

F1⁽F1_RL1, ...)

24V 460mA

D D

C C

B B

A A

Neopixel_Driver.SchDoc

SHEET

Expatria Technologies

625 Kane Valley Rd.
Box 2084

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

REV

MODIFIED | SHEET
11 27 /

AM

ENGR DOCUMENT

B9

PROJECT
Longboard_32bit_ext.PrjPCB

Merritt, BC V1K1B8

LED_CONTROL

1

1

2

2

P19

DB2EVC-3.81-2P-GN

1

1
2

2
3

3

J21

B3B-XH-A(LF)(SN) VDD 1

DOUT | 2
VSS | 3

DIN 4

U28

C95 | WS2812B-B/W
100nF

VCC_SYS_5V0

LED_CONTROL_OUT

LED_POWER_OUT

## Neopixel Driver

2

1

J32

WJ15EDGK-3.81-2P

LED_CONTROL_OUT

VDD1 1
| VOA | 7
VIB 3
GND1 4 | GND2 | 5
| VOB | 6

VIA 2

VDD2 8

U14

ADUM1200ARZ-RL7

C68

100nF

C67

100nF

VCC_MCU_3V3

VCC_SYS_5V0

RING_LED_CTRL

RING_LED_OUT

1

1
2

2
3

3

J18

B3B-XH-A(LF)(SN)

VCC_SYS_5V0 | R101 | 0Ω ±1%
| R100 | DNI

PA13

PC9

R97
200Ω ±1%
R96
200Ω ±1%

R28
200Ω ±1%

C5

1uF | 1
| 2

P5

Header 2

VCC_SYS_24V0

VCC_SYS_24V0

This page includes a Neopixel LED that is the first in the chain.

D D

C C

B B

A A

External_Stepper.SchDoc

SHEET

Expatria Technologies

625 Kane Valley Rd.
Box 2084

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

REV

MODIFIED | SHEET
12 27 /

AM

ENGR DOCUMENT

B9

PROJECT
Longboard_32bit_ext.PrjPCB

Merritt, BC V1K1B8

AL_A_n

DIR_A

EN_A

STEP_A

R114
220Ω ±1%

U29

EL357N(B)(TA)-G

R113
220Ω ±1%

VCC_SYS_5V0

STEP_A_EXT

R116
220Ω ±1%

U30

EL357N(B)(TA)-G

R115
220Ω ±1%

VCC_SYS_5V0

DIR_A_EXT

R118

220Ω ±1%

U31

EL357N(B)(TA)-G

R117
220Ω ±1%

VCC_SYS_5V0

EN_A_EXT

3

1
4

2

6 5
8 7

P20

C9135

STP_ALARM_5V_n

## External Stepper

STEP_A_EXT
DIR_A_EXT
EN_A_EXT

U32

EL357N(B)(TA)-G

STP_ALARM_5V_n

R120

510Ω ±1%

VCC_SYS_5V0 R119
4.7KΩ ±1%

VCC_MCU_3V3

C96
100nF

STEP_A_EXT

DIR_A_EXT

EN_A_EXT

STP_ALARM_5V_n

D37
0603 LED Green

R160
2.2KΩ ±1%

VCC_MCU_3V3

D38
0603 Red

R161
2.2KΩ ±1%

VCC_MCU_3V3
Q8
MMBT5551

R98

10KΩ ±1%

R172
4.7KΩ ±1%

R171
4.7KΩ ±1%

R170
4.7KΩ ±1%

D D

C C

B B

A A

5V_Digital_Out.SchDoc

SHEET

Expatria Technologies

625 Kane Valley Rd.
Box 2084

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

REV

MODIFIED | SHEET
13 27 /

AM

ENGR DOCUMENT

B9

PROJECT
Longboard_32bit_ext.PrjPCB

Merritt, BC V1K1B8

3V_INPUT

R122 ⁽R122_AO0, ...)

220Ω ±1%

U33 ⁽U33_AO0, ...)

EL357N(B)(TA)-G

R121⁽R121_AO0, ...)
120Ω ±1%

VCC_SYS_5V0

5V_OUT

## 5V Isolated Output

R77 ⁽R77_AO0, ...)
10KΩ ±1%

D D

C C

B B

A A

3V3_Digital_Out.SchDoc

SHEET

Expatria Technologies

625 Kane Valley Rd.
Box 2084

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

REV

MODIFIED | SHEET
14 27 /

AM

ENGR DOCUMENT

B9

PROJECT
Longboard_32bit_ext.PrjPCB

Merritt, BC V1K1B8

5V_INPUT

R124 ⁽R124_N0, ...)

510Ω ±1%

U34 ⁽U34_N0, ...)

EL357N(B)(TA)-G

R123 ⁽R123_N0, ...)
1KΩ ±1%
3V3_OUT

## 3.3V Isolated Output

VCC_MCU_3V3

C107 ⁽C107_N0, ...)
100nF

D D

C C

B B

A A

Transistor_Driver.SchDoc

SHEET

Expatria Technologies

625 Kane Valley Rd.
Box 2084

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

REV

MODIFIED | SHEET
15 27 /

AM

ENGR DOCUMENT

B9

PROJECT
Longboard_32bit_ext.PrjPCB

Merritt, BC V1K1B8

TRN_DRIVE

D31⁽D31_TR1, ...)
B5819W SL | 1

1

| 2

2

P21⁽P21_TR1, ...)

DB2EVC-3.81-2P-GN

## Transistor Driver

2

1

J33 ⁽J33_TR1, ...)

WJ15EDGK-3.81-2P
4

6
1

2

NC 3

5

K1⁽K1_TR1, ...)

TLP3109A(TP,F

R39 ⁽R39_TR1, ...)

1.5KΩ ±1%

5V through 100R

D15 ⁽D15_TR1, ...)
0603 LED Green

R33 ⁽R33_TR1, ...)
4.7KΩ ±1%

VCC_SYS_5V0

R174 ⁽R174_TR1, ...)
10KΩ ±1%

1 3 2

Q9 ⁽Q9_TR1, ...)
2N7002-7-F

F2 ⁽F2_TR1, ...)

24V 1A

D D

C C

B B

A A

Misc_switches.SchDoc

SHEET

Expatria Technologies

625 Kane Valley Rd.
Box 2084

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

REV

MODIFIED | SHEET
16 27 /

AM

ENGR DOCUMENT

B9

PROJECT
Longboard_32bit_ext.PrjPCB

Merritt, BC V1K1B8

OUTPUT LED-

LED+

ISO_3.3V LIMIT_AN
LIMIT_K

CY
Photocoupler12Vinput.SchDoc

OUTPUT

LED+
LED-

ISO_3.3V LIMIT_AN
LIMIT_K

MC1
Photocoupler12Vinput.SchDoc

OUTPUT

LED+
LED-

ISO_3.3V LIMIT_AN
LIMIT_K

HL
Photocoupler12Vinput.SchDoc

## Misc Switches

R20
1KΩ ±1%

D10
0603 Yellow

R18
1KΩ ±1%

VCC_MCU_3V3

VCC_MCU_3V3

VCC_MCU_3V3

Macro1

HALT

Start

Macro2

R21
1KΩ ±1%

D13
0603 Red

OUTPUT

LED+
LED-

ISO_3.3V LIMIT_AN
LIMIT_K

MC2
Photocoupler12Vinput.SchDoc D11 0603 Yellow

R19
1KΩ ±1%

VCC_MCU_3V3

Macro1_ext

Macro2_ext

Start_ext

HALT_ext

VCC_SYS_5V0

VCC_SYS_5V0

VCC_SYS_5V0

VCC_SYS_5V0

MAC3 (SW and SILK)

MAC1 (SW and SILK)

MAC2 (SW and SILK)

D12
0603 Yellow

D D

C C

B B

A A

Photocoupler12Vinput.SchDoc

SHEET

Expatria Technologies

625 Kane Valley Rd.
Box 2084

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

REV

MODIFIED | SHEET
17 27 /

AM

ENGR DOCUMENT

B9

PROJECT
Longboard_32bit_ext.PrjPCB

Merritt, BC V1K1B8

U2 ⁽U2_AL, ...)

EL357N(B)(TA)-G

OUTPUT

R23 ⁽R23_AL, ...)

1KΩ ±1%

R22 ⁽R22_AL, ...)
4.7KΩ ±1%

## Coupler 12V input

C3 ⁽C3_AL, ...)
100nF

LED+
LED-LIMIT_AN

ISO_3.3V

LIMIT_K

D D

C C

B B

A A

2024-06-09 9:13:38 AM

Limit_Switches.SchDoc

SHEET

Expatria Technologies

625 Kane Valley Rd.
Box 2084

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

REV

MODIFIED | SHEET
18 27 /

AM

ENGR DOCUMENT

B9

PROJECT
Longboard_32bit_ext.PrjPCB

Merritt, BC V1K1B8

X_LIM

Y1_Lim

## Limit Switches

D5
0603 Yellow

R13
1KΩ ±1%

VCC_MCU_3V3

D6
0603 Yellow

R14
1KΩ ±1%

VCC_MCU_3V3

D7
0603 Yellow

R15
1KΩ ±1%

VCC_MCU_3V3

D8
0603 Yellow

R16
1KΩ ±1%

VCC_MCU_3V3

D9
0603 Yellow

R17
1KΩ ±1%

VCC_MCU_3V3

X_LIM_ext

Y_LIM_ext

A_LIM_ext

Probe_TLO

Probe

D4
0603 Yellow

R12
1KΩ ±1%

VCC_MCU_3V3

OUTPUT

LED+
LED-

ISO_3.3V LIMIT_AN
LIMIT_K

TLO
Photocoupler12Vinput.SchDoc | D3
| 0603 Yellow
| R11
| 1KΩ ±1%

VCC_MCU_3V3
PRB_TLO_ext

PROBE_ext

A_Lim

LIMIT_VCC_SEL

LIMIT_VCC_SEL

LIMIT_VCC_SEL

LIMIT_VCC_SEL

LIMIT_VCC_SEL

LIMIT_VCC_SEL

LIMIT_VCC_SEL

OUTPUT

LED+
LED-

ISO_3.3V LIMIT_AN
LIMIT_K

PRB
Photocoupler12Vinput.SchDoc

OUTPUT

LED+
LED-

ISO_3.3V LIMIT_AN
LIMIT_K

XL
Photocoupler12Vinput.SchDoc

OUTPUT

LED+
LED-

ISO_3.3V LIMIT_AN
LIMIT_K

Y1L
Photocoupler12Vinput.SchDoc

OUTPUT

LED+
LED-

ISO_3.3V LIMIT_AN
LIMIT_K

Y2L
Photocoupler12Vinput.SchDoc

OUTPUT

LED+
LED-

ISO_3.3V LIMIT_AN
LIMIT_K

ZL
Photocoupler12Vinput.SchDoc

OUTPUT

LED+
LED-

ISO_3.3V LIMIT_AN
LIMIT_K

AL
Photocoupler12Vinput.SchDoc

LIMIT_VCC_SEL

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
XH-4A

INPUT_GND

INPUT_GND

INPUT_GND

R10

DNI

R9

0Ω ±1% | LIMIT_VCC_SEL

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
XH-4A

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
XH-4A

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
XH-4A

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
XH-4A

VCC_SYS_5V0

LIMIT_VCC_SEL INPUT_GND

LIMIT_VCC_SEL

LIMIT_VCC_SEL

LIMIT_VCC_SEL

LIMIT_VCC_SEL

INPUT_GND

INPUT_GND

INPUT_GND

INPUT_GND

Mating Plug: XHP-4

VCC_SYS_24V0

X_LIM_ext
Y_LIM_ext

A_LIM_ext

LIMIT_VCC_SEL

INPUT_GND

1

2

3

P7

WJ15EDGK-3.81-3P

2

1

J35

WJ15EDGK-3.81-2P

1

1

2

2

J3

WJ15EDGRC-3.81-2P

1

1

2

2

3

3

J2

WJ15EDGRC-3.81-3P

D39
0603 Yellow

R63
1KΩ ±1%

VCC_MCU_3V3
DOOR_ext

DOOR

LIMIT_VCC_SEL

OUTPUT

LED+
LED-

ISO_3.3V LIMIT_AN
LIMIT_K

DR

### 1 Photocoupler12Vinput.SchDoc 1

2

2
3

3
4

4

J15

XH-4A

LIMIT_VCC_SEL INPUT_GND
DOOR_IN_5V

Z_LIM_ext

Y2_LIM_ext

Z_LIM

Y2_LIM

Z_LIM

Y2_Lim

X_LIM

Y_LIM

A_LIM

PRB_TLO

PROBE

DOOR

Y2_LIM_ext

Z_LIM_ext

1

J36

WJ15EDGK-3.81-7P

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
DB2EVC-3.81-7P-GN

D D

C C

B B

A A

2024-06-09 9:13:38 AM

DC_Power_Regulation.SchDoc

SHEET

Expatria Technologies

625 Kane Valley Rd.
Box 2084

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

REV

MODIFIED | SHEET
19 27 /

AM

ENGR DOCUMENT

B9

PROJECT
Longboard_32bit_ext.PrjPCB

Merritt, BC V1K1B8

## DC Power Regulation

VCC_SYS_24V0

VCC_SYS_5V0

VCC_MCU_5V0

D23
1SMAF4734A

R82
10KΩ ±1%

POWER_OUT_5V

PWR_IN_24V

ENABLE_5V

5V_Supply
5V_Power_Supply.SchDoc

VCC_SYS_5V0

L8

220R @ 100Mhz 2A
C55
22uF

C54
4.7uF

VCC_MCU_5V0

C56
100uF

D20
0603 LED Green

L9

220R @ 100Mhz 2A

C57
100uF

Vin Vout GND

VR1

AMS1117-3.3

C59
10uF

C58
10uF

VCC_MCU_3V3

VCC_MCU_5V0

These are connected through mushroom. Breaking it cuts motor power.

R83
10KΩ ±1%

D24
0603 LED Green

Macro1_ext
Macro2_ext
Start_ext

HALT_ext

INPUT_VCC
VCC_SYS_5V0

R38
10KΩ ±1%

This switch will turn off all power by disabling 24V supply.

PWR_EN

C113
100nF

1

2

P23

Header 2 Mushroom Bypass

Power supplied for indication LED.

2

1

3

S1

SS-12D11G5R

2

1

640456-2

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
MX15EDGR-3.81-GN01-07P-Cu-A

ESTOP_5V_EN

D32
0805 LED Red

VCC_SYS_5V0

R111
1KΩ ±1%
MOTOR_nPGD | 1 | 3 2

Q3
2N7002-7-F

ENABLE_5V

POWER_OUT_24V

PWR_IN_36-80V

24V_Supply
D14 | 24V_Power_Supply.SchDoc

SS210

PWR_EN

L7
220R @ 100Mhz 2A
DC_IN | POWER_OUT_36-80V

24V_Relay

VCC_5V | MOTOR_nPGD
ESTOP_EN | CURRENT_SENSE

DC_SW
DC_Power_Switching.SchDoc
MOTOR_VCC_80V

VCC_SYS_24V0

Main Power Input INPUT_VCC

C90
10uF

C89
10uF

2

1

P10

DB2ERC-5.08-2P-GN | VCC_SYS_24V0

VCC_SYS_5V0

VCC_SYS_5V0

MOTOR_UNVLO_ES

ESTOP_5V_EN

L12
220R @ 100Mhz 2A MOTOR_nPGD

U43

EL357N(B)(TA)-G

VCC_SYS_24V0

R184

5.1KΩ ±1%

MOTOR_VCC_80V

VCC_SYS_5V0

ESTOP_5V_EN

R196
1KΩ ±1%

Enable should be left
unconnected if unused.

D D

C C

B B

A A

2024-06-09 9:13:38 AM

5V_Power_Supply.SchDoc

SHEET

Expatria Technologies

625 Kane Valley Rd.
Box 2084

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

REV

MODIFIED | SHEET
20 27 /

AM

ENGR DOCUMENT

B9

PROJECT
Longboard_32bit_ext.PrjPCB

Merritt, BC V1K1B8

BOOT 1
VIN 2
EN 3
SS 4 | VSENSE | 5
| COMP | 6
| GND | 7
| PH | 8

U16

TPS54331DR

L3

### 22 uH

C10

100nF

C16
10nF

C11
10uF

C12
10uF

C13
22uF

C14
10uF

C15
10uF

C18
8.2nF
C19
8.2nF

C17
10pF

D19
SS54

R55
10KΩ ±1% R56
47KΩ ±1%

PWR_IN_24V

POWER_OUT_5V

## 5V Power Supply

C52
22uF

C53
22uF

# 4.98V output

ENABLE_5V | R57 1.91KΩ ±1%

Pin3 should be floating if unused.

D D

C C

B B

A A

2024-06-09 9:13:38 AM

24V_Power_Supply.SchDoc

SHEET

Expatria Technologies

625 Kane Valley Rd.
Box 2084

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

REV

MODIFIED | SHEET
21 27 /

AM

ENGR DOCUMENT

B9

PROJECT
Longboard_32bit_ext.PrjPCB

Merritt, BC V1K1B8

C74

10uF 100V PWR_IN_36⁻80V

POWER_OUT_24V

## 24V Power Supply

# 24.03V output

ENABLE_5V

C69

100nF 100V

4 1 5 2

3

6

7

8
Q14
CSD19538Q3A

L5

68uH ±20%

VCC 14

VIN 20

BST | 17
COMP | 4

EN/UVLO 1

EP | 15 Exposed Pad | 21
FB | | 5
HO | 18
ILIM | 11
LO | 13

PGOOD 10

RT 2

SS/TRK 3

SW 19

SYNCIN 8

SYNCOUT 7

NC 9

NC 16 | AGND | 6
| PGND | 12

U24

LM5146QRGYTQ1

C76
100nF 100V

R30
180KΩ ±1%

R43
8.2KΩ ±1%

R29

2.2Ω ±1%

4 1 5 2

3

6

7

8
Q15
CSD19538Q3A

R125

20KΩ ±1%

R132

20KΩ ±1%

C75
2.2uF 100V

R134
2.2Ω ±1% | C81 100nF 100V

C77
10uF

C78
10uF

C79
10uF

C80
10uF

R167

1.5KΩ ±1%

C84
5.6pF

R176
18KΩ ±1%

R178
620Ω ±1%

R175
4.7Ω ±1%

C83
1.5nF

C85

8.2nF
C86

220pF

R177
5.1KΩ ±1%

R179
39KΩ ±1%

C145
10uF 100V

C144
10uF 100V

C115
10uF 100V

D D

C C

B B

A A

2024-06-09 9:13:38 AM

DC_Power_Switching.SchDoc

SHEET

Expatria Technologies

625 Kane Valley Rd.
Box 2084

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

REV

MODIFIED | SHEET
22 27 /

AM

ENGR DOCUMENT

B9

PROJECT
Longboard_32bit_ext.PrjPCB

Merritt, BC V1K1B8

POWER_OUT_36-80V

## Main Switch and OCP

Main Power Input INPUT_VCC

MOTOR_VCC_80V

C88
10uF

C87
10uF

R126
0.003Ω ±1%

DC_IN

Rs for OCP

R128
4.7Ω ±1%

COM 30

NO

85 | CL2 | 87
CL1 86

NC 87a

K2

VCF4-1000

24V_Relay

D46
85V TVS

D48
SS210

D47

SS210
R129

100Ω ±1%

C91

10uF 100V

1 2

R159

B57235S0100M000
20R NTC total

Q13
ST3422A

D45
SS210

1 2 34

5

+

- U41

INA280A3IDCKR

VCC_5V
C92
4.7uF

RELAY_GATE

5V_VCC

C94
10uF

R130
10KΩ ±1%

R133
24KΩ ±1%

5V_VCC

OCP1_THRS

ESTOP_EN
C99
4.7uF

C103
10uF | D49
| ZMM5V6-M

R180
2.2KΩ ±1%

R173
510KΩ ±1%

C93
100nF

3.03V at 10A

R182
DNI

3

2

### 1 ⁸ 4

U40A
LM393DR2G

C104

100nF

5V_VCC

5

6

### 7 ⁸ 4

U40B
LM393DR2G

5V_VCC

R163

100KΩ ±1%

C105
100nF

ESTOP_EN

ESTOP_EN

FAULT2

3.51V at 11.7A

D50
85V TVS

FAULT1_n

R183
100KΩ ±1%

R42
0Ω ±1%
C106

470nF

1

2

4

GND 3

VCC 5

U44

SN74LVC1G32DCKR

5V_VCC

RELAY_GATE_n

C108

100nF

5V_VCC

1

2

3

U42A

SN74HC00DR

4

5

6

U42B

SN74HC00DR

10

8

9

U42C

SN74HC00DR

11

12

13

U42D

SN74HC00DR

VCC 14 | GND | 7

U42E

SN74HC00DR

5V_VCC

1

1

2

2

P6

DB2EVC-3.81-2P-GN

WSF50P10 P MOSFET Q1

NTC_BYP_GATE

TRIG 2

OUT 3

RST 4

CVOLT 5

THR 6
DISC | 7
VCC | 8

GND 1

U50

NE555DR

4

1

2

U25A

74LVC1G08GW,125

VCC 5 | GND | 3

U25B

C140 | SN74LVC1G08GW
100nF

5V_VCC

Q16
BSS123

R197
10KΩ ±1%

D56

B5819W SL

RELAY_GATE

R198
4.7KΩ ±1%

RELAY_GATE

R199

470KΩ ±1%

C139
4.7uF

5V_VCC

C141

1uF

R200
1KΩ ±1%

C142
100nF

RELAY_ACT

RELAY_ACT

Q17
BSS123
R202
10KΩ ±1%

5V_VCC

RELAY_GATE

R201

330KΩ ±1%

C143
22uF

INPUT_INRUSH

D58
0603 Red

R204
1KΩ ±1%

D57
0603 LED Blue

R203
1KΩ ±1%

R127
DNI

R213

2.2KΩ ±1%

1 2
D36
MM3Z10VST1G

R106

3.3KΩ ±1%

R162
3.3KΩ ±1%

NTC_BYP_GATE

R103
4.7KΩ ±1%

R209
0Ω ±1%

R210
0Ω ±1%

FAULT1+

FAULT1-

CURRENT_SENSE CURRENT_SENSE

FAULT1+

FAULT1-

R211

0Ω ±1%

R212

DNI

R215
DNI

FAULT1+

FAULT1-

TIMER_OUT

MOTOR_nPGD

TIMER_OUT

RELAY_GATE_n

R181
10KΩ ±1%

OCP1_THRS

CURRENT_SENSE

F3
24V 460mA

1 2

R104

B57235S0100M000

R70
100Ω ±1%

QUAD-NAND forms latching fault switch, reset by re-enabling etsop.

Estop enable is connected from system 5V and is filtered here.

Enable Lockout should have a time constant of 10s

2nd channel not currently used.

Rework here for first

### 50 boards is to drop a

16.7K resistor onto
R130, but BOM
change is on R133 to
24K.

D D

C C

B B

A A

2024-06-09 9:13:38 AM

Spindle_Control.SchDoc

SHEET

Expatria Technologies

625 Kane Valley Rd.
Box 2084

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

REV

MODIFIED | SHEET
23 27 /

AM

ENGR DOCUMENT

B9

PROJECT
Longboard_32bit_ext.PrjPCB

Merritt, BC V1K1B8

## Spindle Control

R35

220Ω ±1%

U7

EL357N(B)(TA)-G

U4

EL357N(B)(TA)-G

R25

220Ω ±1%

SPINDLE_PWM

R31
220Ω ±1%

U5

EL357N(B)(TA)-G

SPINDLE_DIR

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
DB2EVC-3.81-5P-GN

SPIN_DIR_12V
SPIN_EN_12V

SPINDLE_CONN

R32

220Ω ±1%

U6

EL357N(B)(TA)-G

SPINDLE_EN

R34
300Ω ±1%

VCC_SYS_5V0

LASER_EN

SPINDLE_DIR

SPINDLE_PWM

R37

220Ω ±1%

U8

EL357N(B)(TA)-G

R41
220Ω ±1%

U10

EL357N(B)(TA)-G

VCC_SYS_5V0

VCC_SYS_5V0

J27

WJ15EDGK-3.81-5P

1

2

3

P22

WJ15EDGK-3.81-3P

SPINDLE_AT_SPEED

LASER_EN_ext

LASER_PWM_ext

SPIN_AT_SPEED

1

1
2

2
3

3

J11

WJ15EDGRC-3.81-3P

D2
0603 White
1 3 2

Q4
2N7002-7-F

R151
4.7KΩ ±1%

SPINDLE_PWM

VCC_MCU_5V0

D28
0603 Red
1 3 2

Q5
2N7002-7-F

R152
4.7KΩ ±1%

VCC_MCU_5V0

Laser_PWM

Laser_PWM

R153
10KΩ ±1%

R154
10KΩ ±1%

R165
510Ω ±1%

U23

EL357N(B)(TA)-G

R164
4.7KΩ ±1%

VCC_MCU_3V3

C73
100nF

1 3 2

Q11
2N7002-7-F

VCC_MCU_3V3

R84
10KΩ ±1%

SPIN_EN

VCC_MCU_3V3

SPINDLE_EN_TTL | SPINDLE_EN_TTL

SPIN_EN

SPIN_EN

1 3 2

Q12
R166 | 2N7002-7-F
10KΩ ±1%

LASER_PWM

R99
DNI

GND 2 VCC 5

U3C

C4 | SN74LVC2G17DBVR
100nF

VCC_SYS_5V0

VCC_SYS_5V0

R169
10KΩ ±1%

R168
10KΩ ±1%

R26
10KΩ ±1%

R24

220Ω ±1%

R36

220Ω ±1%

R40
220Ω ±1% | 1 | 6

U3A

SN74LVC2G17DBVR

3 4

U3B

SN74LVC2G17DBVR

D D

C C

B B

A A

2024-06-09 9:13:38 AM

CANBUS_Pendant.SchDoc

SHEET

Expatria Technologies

625 Kane Valley Rd.
Box 2084

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

REV

MODIFIED | SHEET
24 27 /

AM

ENGR DOCUMENT

B9

PROJECT
Longboard_32bit_ext.PrjPCB

Merritt, BC V1K1B8

## CANBUS Pendant

PENDANT_VCC_5V0

PENDANT_VCC_5V0

L10

220R @ 100Mhz 100mA

L11
220R @ 100Mhz 100mA

C61
22uF

C60
4.7uF

KPSTR

1
2
3
4
5
6

RJ12 6P6C

J14

KH-PCB-6P6C

TXD 1
GND 2
VCC 3
RXD 4 | Vref | 5
| CANL | 6
CANH | 7
Rs | 8

U19

CAN/PCA82C250T/YM

C64
1uF

PENDANT_VCC_5V0

R95
2KΩ ±1%

R94
2KΩ ±1%

D26
0603 LED Green

D25
0603 Red

VCC_MCU_3V3

CANBUS | CAN_TX

CAN_RX CANBUS

U21

EL357N(B)(TA)-G

U22

EL357N(B)(TA)-G

R90
2KΩ ±1%

R92
2KΩ ±1%

VCC_MCU_3V3

C65 | VCC_MCU_3V3
100nF

C66
100nF

PENDANT_VCC_5V0

R86
47KΩ ±1%

R87
120Ω ±1%

CANH
CANL

HALT_pen

KPSTR_pen

PENDANT_VCC_5V0
R91
2KΩ ±1%

PENDANT_VCC_5V0
R93
2KΩ ±1%

HALT_PENDANT

HALT_pen
KPSTR_pen

VCC_MCU_5V0

VDD1 1
| VIA | 7
VIB 3
GND1 4 | GND2 | 5
| VOB | 6

VOA 2

VDD2 8

U18

CBMuD1201LAS8

C63

100nF

C62

100nF

D42

ZMM3V3-M

VCC_MCU_3V3

PENDANT_VCC_5V0

D41

ZMM5V6-M R88
200Ω ±1%

R85
200Ω ±1%

D D

C C

B B

A A

2024-06-09 9:13:38 AM

USB_Connector.SchDoc

SHEET

Expatria Technologies

625 Kane Valley Rd.
Box 2084

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

REV

MODIFIED | SHEET
25 27 /

AM

ENGR DOCUMENT

B9

PROJECT
Longboard_32bit_ext.PrjPCB

Merritt, BC V1K1B8

CC1 | A5
DP1 | A6
DN1 | A7
SBU1 | A8

VBUS A4B9
VBUS B4A9

SBU2 B8
DN2 B7
DP2 B6
CC2 B5

SHIELD S1
SHIELD S2
SHIELD S3
SHIELD S4
GND A1B12
GND B1A12

J20

TYPE-C-31-M-12

R108
4.7KΩ ±1%

R107
4.7KΩ ±1%

USBC_CC1

USBC_CC2

USBC_CC2 | USBC_CC1

1

2

3 4

5

6

D27

USBLC6-2SC6

## USBC MCU Connector

USB_MCU | USB_D_P USB_D_N
USB2 | VBUS

CONN_USB_D_P

CONN_USB_D_N | CONN_USB_D_N
CONN_USB_D_N | CONN_USB_D_P

CONN_USB_D_P

CONN_USB_D_N

CONN_USB_D_P

1

3 4

2

L13

DLW21HN900SQ2L

i

D90_NET

i

D90_NET

i

D90_NET

i

D90_NET

D D

C C

B B

A A

2024-06-09 9:13:38 AM

RS485.SchDoc

SHEET

Expatria Technologies

625 Kane Valley Rd.
Box 2084

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

REV

MODIFIED | SHEET
26 27 /

AM

ENGR DOCUMENT

B9

PROJECT
Longboard_32bit_ext.PrjPCB

Merritt, BC V1K1B8

## RS485_Spindle

C9
1uF

RO 1
RE 2
DE 3
DI 4
GND | 5
A | 6

B

7

VCC 8

U13

SN75176BDR

R49
130Ω ±1%

B
A

RE
DE | 1

1

2

2

3

3

D16
SM712

R46
560Ω ±1%

R48
560Ω ±1%

RE TXD

RXD | TXD RXD
VCC_SYS_5V0 | VCC_SYS_5V0_RS485

L1

220R @ 100Mhz 100mA

L2

220R @ 100Mhz 100mA

C8
22uF

C7
4.7uF

DIR

U15

EL357N(B)(TA)-G

R51
220Ω ±1%

DIR

VCC_SYS_5V0_RS485

VCC_SYS_5V0_RS485
VCC_SYS_5V0_RS485

R54
2KΩ ±1%

R53
2KΩ ±1%

D18
0603 LED Green

D17
0603 Red

VCC_MCU_3V3

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
WJ15EDGK-3.81-4P

VCC_SYS_5V0_RS485

VDD1 1
| VIA | 7
VIB 3
GND1 4 | GND2 | 5
| VOB | 6

VOA 2

VDD2 8

U12

CBMuD1201LAS8

C135

100nF

C134

100nF

RO
DI

D1
ZMM3V3-M

R50
200Ω ±1%

VCC_SYS_5V0_RS485

VCC_MCU_3V3

D40
ZMM5V6-M

VCC_SYS_5V0_RS485

1
2
3
4
5
6

RJ12 6P6C

J12

KH-PCB-6P6C

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
DB2EVC-3.81-4P-GN

R52
2KΩ ±1%

R45
200Ω ±1%

R44
200Ω ±1%

R47
2KΩ ±1%

VCC_SYS_5V0_RS485

D D

C C

B B

A A

2024-06-09 9:13:38 AM

Change Log.SchDoc

SHEET

Expatria Technologies

625 Kane Valley Rd.
Box 2084

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

REV

MODIFIED | SHEET
27 27 /

AM

ENGR DOCUMENT

B9

PROJECT
Longboard_32bit_ext.PrjPCB

Merritt, BC V1K1B8

Date | Description Revision
2/14/24 | B6

# Change Log

Date | Description Revision

## Change Log

Initial commit of original SLB files to be modified.

03/27/24 B7

Update power supply and other changes

4/1/24 | B8

BOM updates for availability Footprint and 3d model updates

6/9/24 | B9

Added series reseistor to OCP and updated component values.

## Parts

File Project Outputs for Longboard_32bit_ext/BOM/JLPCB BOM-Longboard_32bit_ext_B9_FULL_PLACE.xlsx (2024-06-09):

Quantity | Manufacturer Part Number | Manufacturer | Description | SuppliersPartNumber | Designator | Comment
30 | CC0603KRX7R9BB104 | YAGEO | 50V 100nF X7R ±10% 0603 Multilayer Ceramic Capacitors MLCC - SMD/SMT ROHS, Chip capacitors | C14663 | C1, C2, C4, C6, C10, C41, C42, C43, C44, C45, C47, C48, C49, C50, C65, C66, C67, C68, C93, C95, C104, C105, C108, C113, C116, C119, C122, C136, C140, C142 | 100nF
48 | CL05B104KO5NNNC | Samsung Electro-Mechanics | 16V 100nF X7R ±10% 0402 Multilayer Ceramic Capacitors MLCC - SMD/SMT ROHS | C1525 | C3_AL, C3_CY, C3_DR, C3_HL, C3_MC1, C3_MC2, C3_PRB, C3_TLO, C3_XL, C3_Y1L, C3_Y2L, C3_ZL, C21, C22, C24, C29, C30, C31, C32, C33, C34, C35, C36, C37, C51, C62, C63, C70, C71, C72, C73, C96, C102, C107_N0, C107_N1, C107_N2, C107_N3, C125, C126, C127, C128, C129, C130, C133, C134, C135, C137, C138 | 100nF
9 | CL10A105KB8NNNC | Samsung Electro-Mechanics | Chip capacitors | C15849 | C5, C9, C27, C28, C40, C46, C64, C98, C141 | 1uF
2 | CL21A475KAQNNNE | Samsung Electro-Mechanics | Chip capacitors | C1779 | C7, C60 | 4.7uF
8 | CL21A226MAQNNNE | Samsung Electro-Mechanics | 25V 22uF X5R ±20% 0805 Multilayer Ceramic Capacitors MLCC - SMD/SMT ROHS | C45783 | C8, C13, C52, C53, C55, C61, C123, C131 | 22uF
14 | CL31A106KBHNNNE | Samsung Electro-Mechanics | 50V 10uF X5R ±10% 1206 Multilayer Ceramic Capacitors MLCC - SMD/SMT ROHS | C13585 | C11, C12, C14, C15, C58, C59, C77, C78, C79, C80, C87, C88, C89, C90 | 10uF
1 | 0603B103K500NT | Guangdong Fenghua Advanced Tech | 50V 10nF X7R ±10% 0603 Multilayer Ceramic Capacitors MLCC - SMD/SMT ROHS | C57112 | C16 | 10nF
3 | CL10C100JB8NNNC | Samsung Electro-Mechanics | Chip capacitors | C1634 | C17, C38, C39 | 10pF
4 | CC0603KRX7R9BB822 | YAGEO | 50V 8.2nF X7R ±10% 0603 Multilayer Ceramic Capacitors MLCC - SMD/SMT ROHS | C113812 | C18, C19, C20, C85 | 8.2nF
9 | CL10A475KO8NNNC | Samsung Electro-Mechanics | 16V 4.7uF X5R ±10% 0603 Multilayer Ceramic Capacitors MLCC - SMD/SMT ROHS | C19666 | C23, C25, C26, C54, C92, C99, C100, C124, C132 | 4.7uF
1 | TAJB107K006RNJ | AVX | Tantalum capacitor | C16133 | C56 | 100uF
1 | HV101M035E077ETR | Capxon International Elec | -45℃~+105℃ 2000hrs@105℃ 100uF 7.7mm 35V 6.3mm ±20% SMD,6.3x7.7mm Aluminum Electrolytic Capacitors - SMD ROHS | C59934 | C57 | 100uF
3 | 0805B104K101NT | Guangdong Fenghua Advanced Tech | Chip capacitors | C89258 | C69, C76, C81 | 100nF 100V
5 | GRM32EC72A106KE05L | Murata | Chip capacitors | C576517 | C74, C91, C115, C144, C145 | 10uF 100V
1 | CL31A225KBHNNNE | Samsung Electro-Mechanics | Chip capacitors | C170101 | C75 | 2.2uF 100V
2 | CL05A105KA5NQNC | Samsung Electro-Mechanics | Chip capacitor | C52923 | C82, C101 | 1.0uF
1 | 0603B152K500NT | Guangdong Fenghua Advanced Tech | Chip capacitors | C1595 | C83 | 1.5nF
1 | GQM1875C2E5R6BB12D | Murata | Chip capacitors | C2297617 | C84 | 5.6pF
1 | CL10B221KB8NNNC | Samsung Electro-Mechanics | Chip capacitors | C1603 | C86 | 220pF
2 | [NoParam], CL10A106KP8NNNC | Samsung Electro-Mechanics | Chip capacitors | C19702 | C94, C103 | 10uF
3 | CL05B103KB5NNNC | Samsung Electro-Mechanics | Chip capacitors | C15195 | C97, C109, C118 | 10nF
1 | CL10B474KA8NNNC | Samsung Electro-Mechanics | Chip capacitors | C1623 | C106 | 470nF
2 | 0402B682K500NT | Guangdong Fenghua Advanced Tech | Chip capacitors | C1542 | C110, C111 | 6.8nF
1 | 0402B223K500NT | Guangdong Fenghua Advanced Tech | Chip capacitors | C1532 | C112 | 22nF
1 | CL31B102KGFNNNE | Samsung Electro-Mechanics | Chip capacitors | C35216 | C114 | 1nF
1 | CL05A475MP5NRNC | Samsung Electro-Mechanics | Chip capacitor | C23733 | C117 | 4.7uF
2 | GRM1555C1H100JA01D | Murata Electronics | Chip capacitors | C76946 | C120, C121 | 10pF
1 | 1206B475K500NT | Guangdong Fenghua Advanced Tech | Chip capacitors | C29823 | C139 | 4.7uF
1 | CL31A226KAHNNNE | Samsung | Chip capacitors | C12891 | C143 | 22uF
2 | ZMM3V3-M | ST(Semtech) | Single 3.1V~3.5V 500mW 3.3V LL-34 Zener Diodes ROHS | C8056 | D1, D42 | ZMM3V3-M
1 | 19-218/T1D-CQ2R2TY/3T | Everlight Elec | White LED | C1322288 | D2 | 0603 White
11 | 19-213/Y2C-CQ2R2L/3T(CY) | Everlight Elec | -40℃~+85℃ 585.5nm~591.5nm Yellow 120° 60mW 0603 Light Emitting Diodes (LED) ROHS | C72038 | D3, D4, D5, D6, D7, D8, D9, D10, D11, D12, D39 | 0603 Yellow
10 | KT-0603R | Hubei KENTO Elec | -40℃~+85℃ Red 0603 Light Emitting Diodes (LED) ROHS | C2286 | D13, D17, D25, D28, D38, D58, D61, D62, D63, D64 | 0603 Red
4 | SS210 | MDD(Microdiode Electronics) | 100V 2A 850mV @ 2A SMA(DO-214AC) Schottky Barrier Diodes (SBD) ROHS | C14996 | D14, D45, D47, D48 | SS210
14 | MHT192UGCT | MEIHUA | 20mA -40℃~+85℃ 515nm~530nm Emerald 120° 60mW 0603 Light Emitting Diodes (LED) ROHS | C389519 | D15_TR1, D15_TR2, D18, D20, D24, D26, D29, D37, D43_RL1, D43_RL2, D51, D52, D59, D60 | 0603 LED Green
1 | SM712 | DOWO | Bidirectional 12V (Max), 7V (Max) 7.5V / 13.3V 10V / 20V 12A(8/20us) SOT-23-3 TVS RoHS | C293966 | D16 | SM712
1 | SS54 | MDD | 40V 5A 550mV@5A | C22452 | D19 | SS54
5 | ZMM5V6 | HXY MOSFET | Single 500mW 5.2V~6V 5.6V LL-34 Zener Diodes ROHS | C5345993 | D21, D22, D40, D41, D49 | ZMM5V6-M
1 | 1SMAF4734A | Shandong Jingdao Microelectronics | 27V ±5% 1W 500nA @ 20.5V SMA(DO-214AC) Zener Diodes RoHS | C169539 | D23 | 1SMAF4734A
1 | USBLC6-2SC6 | TECH PUBLIC | Very low capacitance ESD protection, 3.5 pF, -40 to 125 degC, 6-Pin SOT23, RoHS, Tape and Reel | C2827654 | D27 | USBLC6-2SC6
5 | B5819W SL | Jiangsu Changjing Electronics Technology Co., Ltd. | 40V 600mV@1A 1A SOD-123 Schottky Barrier Diodes (SBD) ROHS | C8598 | D30_RL1, D30_RL2, D31_TR1, D31_TR2, D56 | B5819W SL
1 | NCD0805R1 | Foshan NationStar Optoelectronics | Red 0805 Light Emitting Diodes (LED) ROHS | C84256 | D32 | 0805 LED Red
3 | F.0603.00026/P2-0603B1TS2-06T-001 | TUOZHAN | 5mA -40℃~+85℃ Blue 120° 0603 Light Emitting Diodes (LED) ROHS | C7496819 | D33, D34, D57 | 0603 LED Blue
4 | BAT54S | JSMSEMI | 30V Dual 200mA 800mV@100mA SOT-23 Schottky Barrier Diodes (SBD) ROHS | C916425 | D35, D53, D54, D55 | BAT54S Schottky
1 | MM3Z10VST1G | On Semiconductor | MM3Z10VST1G Zener Diode, 10V 2% 300 mW SMT 2-Pin SOD-323 | ON Semiconductor MM3Z10VST1G | C235983 | D36 | MM3Z10VST1G
2 | SMBJ85CA | BORN | 4.4A 137V 94.4V 85V DO-214AA Electrostatic and Surge Protection (TVS/ESD) ROHS | C2842381 | D46, D50 | 85V TVS
3 |  | Jinrui Electronic Materials Co. | 24V 200mA 100A 460mA - Resettable Fuses ROHS | C5307785 | F1_RL1, F1_RL2, F3 | 24V 460mA
2 |  | Jinrui Electronic Materials Co. | 24V 1A 0.1s 1206 PTC Resettable Fuses RoHS | C369160 | F2_TR1, F2_TR2 | 24V 1A
1 | PZ254-2-08-S | HCTL | 250V 3A Brick nogging Square Pins 2.5mm 260℃@5S 6mm 16P -40℃~+105℃ 2.54mm Black 2.54mm 2x8P SMD,P=2.54mm Pin Headers ROHS | C3294466 | J1 | PZ254-2-08-S
2 | WJ15EDGRC-3.81-3P | Ningbo Kangnex | 3.81mm Green Board Edge/Receptacle-Close Push-Pull,P=3.81mm Pluggable System Terminal Block ROHS | C8406 | J2, J11 | WJ15EDGRC-3.81-3P
1 | WJ15EDGRC-3.81-2P | Ningbo Kangnex | 3.81mm Green Board Edge/Receptacle-Close Push-Pull,P=3.81mm Pluggable System Terminal Block ROHS | C8387 | J3 | WJ15EDGRC-3.81-2P
6 | XH-4A | BOOMELE(Boom Precision Elec) | 1x4P 4P XH 1 2.5mm 4 Phosphor bronze Plugin,P=2.5mm Wire To Board / Wire To Wire Connector ROHS | C37815 | J4, J5, J6, J7, J8, J15 | XH-4A
1 | DB2EVC-3.81-5P-GN | DIBO | 3.81mm Green Board Edge/Receptacle-Close Push-Pull,P=3.81mm Pluggable System Terminal Block ROHS | C395701 | J9 | DB2EVC-3.81-5P-GN
1 | DB2EVC-3.81-4P-GN | DIBO | 3.81mm Green Board Edge/Receptacle-Close Push-Pull,P=3.81mm Pluggable System Terminal Block ROHS | C395697 | J10 | DB2EVC-3.81-4P-GN
2 | KH-PCB-6P6C | Shenzhen Kinghelm Elec | RJ45 RJReceptacle No 1 Shrouded Without LED -45℃~+85℃ Plugin Ethernet Connectors/Modular Connectors (RJ45 RJ11) ROHS | C2683354 | J12, J14 | KH-PCB-6P6C
13 | DB2EVC-3.81-2P-GN | DIBO | 3.81mm Green Board Edge/Receptacle-Close Push-Pull,P=3.81mm Pluggable System Terminal Block ROHS | C395686 | J13, J17, P1, P2, P3, P4, P6, P18_RL1, P18_RL2, P19, P21_TR1, P21_TR2, P28 | DB2EVC-3.81-2P-GN
7 | WJ15EDGK-3.81-2P | Ningbo | 2 1 3.81mm Green Plug P=3.81mm Pluggable System Terminal Block ROHS | C8466 | J16, J31_RL1, J31_RL2, J32, J33_TR1, J33_TR2, J34 | WJ15EDGK-3.81-2P
2 | B3B-XH-A(LF)(SN) | JST Sales America | Connector Header Through Hole 3 position 0.098" (2.50mm) | C144394 | J18, J21 | B3B-XH-A(LF)(SN)
1 | TYPE-C-31-M-12 | HRO Electronics Co., Ltd. | USB Connectors 24 Receptacle 1 8.94*7.3mm RoHS | C2765186 | J20 | TYPE-C-31-M-12
1 | WJ15EDGK-3.81-5P | Ningbo Kangnex Elec | 3.81mm Green Plug P=3.81mm Pluggable System Terminal Block ROHS | C3804 | J27 | WJ15EDGK-3.81-5P
1 | WJ15EDGK-3.81-4P | Ningbo | 3.81mm Green Plug P=3.81mm Pluggable System Terminal Block ROHS | C7244 | J28 | WJ15EDGK-3.81-4P
2 | TLP3109A(TP,F | Toshiba | Relay SSR 10mA 1.8V DC-IN 3A 100V DC-OUT 6-Pin 11-7C1S Emboss T/R | C1857559 | K1_TR1, K1_TR2 | TLP3109A(TP,F
1 | VCF4-1000 | TE Connectivity | RELAY SOCKET, 5 PIN, THROUGH HOLE; Available until stocks are exhausted Alternative available | C1519211 | K2 | VCF4-1000
5 | CBG100505U221T | FH (Guangdong Fenghua Advanced Tech) | 700mΩ ±25% 220Ω@100MHz 0402 Ferrite Beads ROHS | C92617 | L1, L2, L4, L10, L11 | 220R @ 100Mhz 100mA
1 | YSPI0630A-220M | YJYCOIN | 3A 22uH ±20% 130mΩ SMD,7.1x6.6x3mm Power Inductors ROHS | C497873 | L3 | 22 uH
1 | HX CYH125-68UH | hanxia | 3A 68uH ±20% 64.8mΩ SMD Inductors (SMD) ROHS | C7587712 | L5 | 68uH ±20%
5 | CBW201209U221T | FH (Guangdong Fenghua Advanced Tech) | 150mΩ ±25% 220Ω@100MHz 0805 Ferrite Beads ROHS | C139188 | L6, L7, L8, L9, L12 | 220R @ 100Mhz 2A
1 | DLW21HN900SQ2L | Murata Electronics | 90Ω@100MHz -40℃~+85℃ 350mΩ 50V 2 330mA 125V SMD-4P Common Mode Filters ROHS | C80529 | L13 | DLW21HN900SQ2L
4 | 22284020 | MOLEX | Straight Square Pins 2 2.54mm Black Brass 1x2P Plugin,P=2.54mm Pin Headers ROHS | C234182 | P5, P23, P25, P26 | Header 2
1 | DB2ERC-5.08-2P-GN | Dibo | 320V 20A 2 Bend -40℃~+105℃ 1 5.08mm 1x2P Green Board Edge/Receptacle-Close Push-Pull,P=5.08mm Pluggable System Terminal Block ROHS | C395737 | P10 | DB2ERC-5.08-2P-GN
1 | 321040SG0ABK00A01 | JILN | 2.54mm Straight Gold Brass 20 Push - Pull 2.54mm 2 Straight,P=2.54mm IDC Connectors ROHS | C601944 | P11 | 321040SG0ABK00A01
1 | HR911105A | DFRobot | HR911105A Ethernet Interface Arduino Platform Evaluation Expansion Board | C163507 | P12 | HR911105A
5 | 2.54-2*4P, C9135 | BOOMELE(Boom Precision Elec), Wurth Electronics | Male Box Header WR-BHD, THT, Vertical, pitch 2.54 mm, 8 pins | C9135 | P13, P14, P16, P20, P27 | C9135
1 | DB2EVC-3.81-7P-GN | DIBO | 3.81mm Green Board Edge/Receptacle-Close Push-Pull,P=3.81mm Pluggable System Terminal Block ROHS | C430333 | P17 | DB2EVC-3.81-7P-GN
1 | MX15EDGR-3.81-GN01-07P-Cu-A | MAX | 300V 8A 7 Bend -40℃~+105℃ 1 3.81mm 1x7P Green Board Edge/Receptacle-Close Push-Pull,P=3.81mm Pluggable System Terminal Block ROHS | C5188162 | P24 | MX15EDGR-3.81-GN01-07P-Cu-A
1 | WSF50P10 | Winsok Semicon | 100V 34A 32mΩ@10V,18A 96W P Channel TO-252-2 MOSFETs ROHS | C2758447 | Q1 | WSF50P10 P MOSFET
3 | ST3422A | STANSON Tech. | 60V 6A 28mΩ@10V,6A 2W 3V@250uA 38pF@15V N Channel 455pF@15V 10nC@10V -55℃~+150℃@(Tj) SOT-23-3L MOSFETs ROHS | C2682907 | Q2_RL1, Q2_RL2, Q13 | ST3422A
11 | 2N7002-7-F | Diodes Inc. | 60V 115mA 7.5Ω@5V,50mA 370mW N Channel SOT-23 MOSFETs ROHS | C85049 | Q3, Q4, Q5, Q6, Q7, Q9_TR1, Q9_TR2, Q10_RL1, Q10_RL2, Q11, Q12 | 2N7002-7-F
1 | MMBT5551 | Jiangsu Changjing Electronics Technology | 50nA 160V 300mW 200@10mA,5V 600mA 100MHz 200mV@50mA,5mA NPN +150℃@(Tj) SOT-23-3 Bipolar Transistors - BJT ROHS | C2145 | Q8 | MMBT5551
2 | CSD19538Q3A | Texas Instruments | CSD19538Q3A 100-V, N channel NexFET™ power MOSFET, single SON 3 mm x 3 mm, 61 mOhm 8-VSONP -55 to 150 | C478471 | Q14, Q15 | CSD19538Q3A
2 | BSS123 | HXY MOSFET | 100V 170mA 6Ω@10V 350mW 2.5V@250uA N Channel SOT-23 MOSFETs ROHS | C5184436 | Q16, Q17 | BSS123
28 | 0402WGF1002TCE | Uniroyal Elec | Chip resistor | C25744 | R1, R5, R6, R7, R26, R27, R61, R62, R77_AO0, R77_AO1, R77_AO2, R77_AO3, R77_COO, R77_MIS, R79, R81, R84, R89_RL1, R89_RL2, R135, R153, R154, R166, R168, R169, R174_TR1, R174_TR2, R194 | 10KΩ ±1%
11 | 0603WAF0000T5E | Uniroyal Elec | Chip resistor | C21189 | R2, R3, R4, R9, R42, R101, R102, R131, R209, R210, R211 | 0Ω ±1%
13 | 0603WAF1002T5E | Uniroyal Elec | Chip resistor | C25804 | R8, R38, R55, R82, R83, R98, R130, R143, R157, R158, R181, R197, R202 | 10KΩ ±1%
16 | 0402WGF1001TCE | Uniroyal Elec | Chip resistor | C11702 | R11, R12, R13, R14, R15, R16, R17, R18, R19, R20, R21, R63, R123_N0, R123_N1, R123_N2, R123_N3 | 1KΩ ±1%
29 | 0402WGF4701TCE | Uniroyal Elec | Chip resistor | C25900 | R22_AL, R22_CY, R22_DR, R22_HL, R22_MC1, R22_MC2, R22_PRB, R22_TLO, R22_XL, R22_Y1L, R22_Y2L, R22_ZL, R33_TR1, R33_TR2, R64, R65, R66, R72, R105_RL1, R105_RL2, R119, R151, R152, R155, R156, R164, R170, R171, R172 | 4.7KΩ ±1%
23 | 0603WAF1001T5E | Uniroyal Elec | Chip resistor | C21190 | R23_AL, R23_CY, R23_DR, R23_HL, R23_MC1, R23_MC2, R23_PRB, R23_TLO, R23_XL, R23_Y1L, R23_Y2L, R23_ZL, R78, R80, R109_RL1, R109_RL2, R111, R193, R195, R196, R200, R203, R204 | 1KΩ ±1%
22 | 0402WGF2200TCE | Uniroyal Elec | Chip resistor | C25091 | R24, R25, R31, R32, R35, R36, R37, R40, R41, R51, R113, R114, R115, R116, R117, R118, R122_AO0, R122_AO1, R122_AO2, R122_AO3, R122_COO, R122_MIS | 220Ω ±1%
10 | 0402WGF2000TCE | Uniroyal Elec | Chip resistor | C25087 | R28, R44, R45, R50, R85, R88, R96, R97, R110, R112 | 200Ω ±1%
2 | 0603WAF220KT5E | Uniroyal Elec | Chip resistor | C22939 | R29, R134 | 2.2Ω ±1%
1 | 0603WAF1803T5E | Uniroyal Elec | Chip resistor | C22827 | R30 | 180KΩ ±1%
1 | 0603WAF3000T5E | Uniroyal Elec | Chip resistor | C23025 | R34 | 300Ω ±1%
2 | 0402WGF1501TCE | Uniroyal Elec | Chip resistor | C25867 | R39_TR1, R39_TR2 | 1.5KΩ ±1%
1 | 0603WAF8201T5E | Uniroyal Elec | Chip resistor | C25981 | R43 | 8.2KΩ ±1%
2 | 0603WAF5600T5E | Uniroyal Elec | Chip resistor | C23204 | R46, R48 | 560Ω ±1%
4 | 0603WAF2001T5E | Uniroyal Elec | Chip resistor | C22975 | R47, R52, R53, R54 | 2KΩ ±1%
1 | 0603WAF1300T5E | Uniroyal Elec | Chip resistor | C22796 | R49 | 130Ω ±1%
1 | 0603WAF4702T5E | Uniroyal Elec | Chip resistor | C25819 | R56 | 47KΩ ±1%
1 | RMC06031.91K1%N | TyoHM | Chip resistor | C325662 | R57 | 1.91KΩ ±1%
1 | 0402WGF5101TCE | Uniroyal Elec | Chip resistor | C25905 | R58 | 5.1KΩ ±1%
7 | 0402WGF5100TCE | Uniroyal Elec | Chip resistor | C25123 | R59, R120, R124_N0, R124_N1, R124_N2, R124_N3, R165 | 510Ω ±1%
12 | 0402WGF2201TCE | Uniroyal Elec | Chip resistor | C25879 | R60, R69, R160, R161, R185, R186, R187, R188, R205, R206, R207, R208 | 2.2KΩ ±1%
5 | 0603WAF220JT5E | Uniroyal Elec | Chip resistor | C23345 | R67, R68, R74, R75, R76 | 22Ω ±1%
1 |  | Uniroyal Elec | Chip resistor | C22775 | R70 | 100Ω ±1%
1 | 0402WGF4702TCE | Uniroyal Elec | Chip resistor | C25792 | R86 | 47KΩ ±1%
1 | 0805W8F1200T5E | Uniroyal Elec | Chip resistor | C17437 | R87 | 120Ω ±1%
6 | 0402WGF2001TCE | Uniroyal Elec | Chip resistor | C4109 | R90, R91, R92, R93, R94, R95 | 2KΩ ±1%
4 | 0603WAF4701T5E | Uniroyal Elec | Chip resistor | C23162 | R103, R107, R108, R198 | 4.7KΩ ±1%
2 | B57235S0100M000 | TDK | Inrush Current Limiter 10 Ohms ±20% 3A 0.374" (9.50mm) | C125456 | R104, R159 | B57235S0100M000
2 | 0603WAF3301T5E | Uniroyal Elec | Chip resistor | C22978 | R106, R162 | 3.3KΩ ±1%
6 | 0402WGF1200TCE | Uniroyal Elec | Chip resistor | C25079 | R121_AO0, R121_AO1, R121_AO2, R121_AO3, R121_COO, R121_MIS | 120Ω ±1%
2 | 0603WAF2002T5E | Uniroyal Elec | Chip resistor | C4184 | R125, R132 | 20KΩ ±1%
1 | WFC12063L000FE66 | Vishay | Chip Resistor | C4286667 | R126 | 0.003Ω ±1%
2 | 0603WAF470KT5E | Uniroyal Elec | Chip resistor | C23164 | R128, R175 | 4.7Ω ±1%
1 | 1206W4F1000T5E | Uniroyal Elec | Chip resistor | C17901 | R129 | 100Ω ±1%
1 |  | Uniroyal Elec | Chip resistor | C23352 | R133 | 24KΩ ±1%
4 | 0402WGF499JTCE | Uniroyal Elec | Chip resistor | C25120 | R136, R137, R144, R145 | 49.9Ω ±1%
4 | 0402WGF330JTCE | Uniroyal Elec | Chip resistor | C25105 | R139, R140, R141, R142 | 33Ω ±1%
1 | 0402WGF100JTCE | Uniroyal Elec | Chip resistor | C25077 | R146 | 10Ω ±1%
1 | 0402WGF1004TCE | Uniroyal Elec | Chip resistor | C26083 | R147 | 1MΩ ±1%
2 | 0402WGF3300TCE | Uniroyal Elec | Chip resistor | C25104 | R148, R150 | 330Ω ±1%
1 | 0402WGF0000TCE | Uniroyal Elec | Chip resistor | C17168 | R149 | 0Ω ±1%
2 | 0603WAF1003T5E | Uniroyal Elec | Chip resistor | C25803 | R163, R183 | 100KΩ ±1%
1 | 0603WAF1501T5E | Uniroyal Elec | Chip resistor | C22843 | R167 | 1.5KΩ ±1%
1 | 0603WAF5103T5E | Uniroyal Elec | Chip resistor | C23192 | R173 | 510KΩ ±1%
1 | 0603WAF1802T5E | Uniroyal Elec | Chip resistor | C25810 | R176 | 18KΩ ±1%
2 | 0603WAF5101T5E | Uniroyal Elec | Chip resistor | C23186 | R177, R184 | 5.1KΩ ±1%
1 | 0603WAF6200T5E | Uniroyal Elec | Chip resistor | C23220 | R178 | 620Ω ±1%
1 | 0603WAF3902T5E | Uniroyal Elec | Chip resistor | C23153 | R179 | 39KΩ ±1%
2 | 0603WAF2201T5E | Uniroyal Elec | Chip resistor | C4190 | R180, R213 | 2.2KΩ ±1%
4 | 0603WAF2000T5E | Uniroyal Elec | Chip resistor | C8218 | R189, R190, R191, R192 | 200Ω ±1%
1 | 0603WAF4703T5E | Uniroyal Elec | Chip resistor | C23178 | R199 | 470KΩ ±1%
1 | 0603WAF3303T5E | Uniroyal Elec | Chip resistor | C23137 | R201 | 330KΩ ±1%
1 | SS-12D11G5R | XKB Connectivity | Shrouded 5A SPDT 125V 125V 5A 10000次 Black Plugin Slide Switches ROHS | C388633 | S1 | SS-12D11G5R
1 | TF-022 | Hanbo Electronic | -40℃~+85℃ 1.28mm Gold plating Deck MicroSD card (TF card) Self bomb SMD SD Card Connectors ROHS | C2962373 | SD3 | TF-022
1 | SN74AHC1G86DBVR | Texas Instruments | XOR (Exclusive OR) IC 1 Channel SOT-23-5 | C7471 | U1 | SN74AHC1G86DBVR
41 | EL357N(B)(TA)-G | Everlight | Optocoupler SOP-4, EL357N(B)(TA)-G, Everlight Electronics | C6649 | U2_AL, U2_CY, U2_DR, U2_HL, U2_MC1, U2_MC2, U2_PRB, U2_TLO, U2_XL, U2_Y1L, U2_Y2L, U2_ZL, U4, U5, U6, U7, U8, U10, U15, U21, U22, U23, U29, U30, U31, U32, U33_AO0, U33_AO1, U33_AO2, U33_AO3, U33_COO, U33_MIS, U34_N0, U34_N1, U34_N2, U34_N3, U39, U43, U47, U48, U49 | EL357N(B)(TA)-G
1 | SN74LVC2G17DBVR | Texas Instruments | Dual Schmitt-Trigger Buffer, DBV0006A, LARGE T&R | C10429 | U3 | SN74LVC2G17DBVR
2 | AM26LS31CDR | Texas Instruments | 4/0 Driver - RS422, RS485 16-SOIC | C6179 | U9, U36 | AM26LS31CDRG4
1 | W5500 | WIZNET | Ethernet Controllers 2.97V ~ 3.63V 10/100 Base-T/TX PHY SPI LQFP-48_7x7x05P Ethernet ICs ROHS | C32843 | U11 | W5500
3 | CBMuD1201LAS8 | Corebai Microelectronics | Dual Channel Isolator | C476472 | U12, U18, U20 | CBMuD1201LAS8
1 | SN75176BDR | Texas Instruments | RS-485/RS-422 | C7063 | U13 | SN75176BDR
7 | ADUM1200ARZ-RL7 | Analog Devices | Dual Channel Isolator | C15219 | U14, U26, U27, U37, U38, U45, U46 | ADUM1200ARZ-RL7
1 | TPS54331DR | Texas Instruments | Switching Voltage Regulators 3A 28V In Step Down SWIFT DC/DC Cnvrtr | C9865 | U16 | TPS54331DR
1 | STM32F412VGT6 | STMicroelectronics | LQFP-100(14x14) Microcontroller Units (MCUs/MPUs/SOCs) ROHS | C727951 | U17 | STM32F412VGT6
1 | PCA82C250T/YM,118 | NXP Semicon | CAN | C7439 | U19 | CAN/PCA82C250T/YM
1 | LM5146QRGYTQ1 | Texas Instruments | Automotive 100-V synchronous buck DC/DC controller with wide duty-cycle range 20-VQFN -40 to 150 | C3188679 | U24 | LM5146QRGYTQ1
1 | 74LVC1G08GW,125 | Nexperia | Single 2-Input Positive-AND Gate, DCK0005A | C12512 | U25 | 74LVC1G08GW,125
1 | WS2812B-B/W | Worldsemi | Intelligent Control LED Integrated Light Source, 3.5 to 5.3 V, -25 to 80 degC, 4-Pin SMD, RoHS, Tape and Reel | C2761795 | U28 | WS2812B-B/W
1 | ZD24C128A-SSGMB | Zetta | IC EEPROM 128KBIT I2C 8SOIC | C918271 | U35 | ZD24C128A-SSGMB
1 | LM393DR2G | onsemi | IC COMPARATOR DUAL OFFSET LV 8SOIC | C7955 | U40 | LM393DR2G
1 | INA280A3IDCKR | Texas Instruments | 2.7-V to 120-V, 1.1-MHz, high-precision current sense amplifier in small (SC-70) package 5-SC70 -40 to 125 | C2868045 | U41 | INA280A3IDCKR
1 | SN74HC00D | Texas Instruments | 4-ch, 2-input, 2-V to 6-V 5.2 mA drive strength NAND gate 14-SOIC -40 to 85 | C10090 | U42 | SN74HC00DR
1 | SN74LVC1G32DCKR | Texas Instruments | 1-ch, 2-input 1.65-V to 5.5-V 32-mA drive strength OR gate 5-SC70 -40 to 125 | C7840 | U44 | SN74LVC1G32DCKR
1 | NE555DR | Texas Instruments | 100kHz SOIC-8 Timers / Clock Oscillators ROHS | C7593 | U50 | NE555DR
1 | AMS1117-3.3 | AMS | Vout=3.3V 1A 72dB@(120Hz) (LDO) | C6186 | VR1 | AMS1117-3.3
1 | TAXM25M4RDBCCT2T | TAE(Zhejiang Abel Elec) | 25MHz 10pF ±10ppm SMD3225-4P Crystals ROHS | C403946 | Y1 | TAXM25M4RDBCCT2T
1 | X322525MSB4SI | Yangxing Tech | 25MHz SMD Crystal Resonator 20pF ±10ppm ±30ppm -40℃~+85℃ SMD3225-4P Crystals ROHS | C13740 | Y3 | X322525MSB4SI

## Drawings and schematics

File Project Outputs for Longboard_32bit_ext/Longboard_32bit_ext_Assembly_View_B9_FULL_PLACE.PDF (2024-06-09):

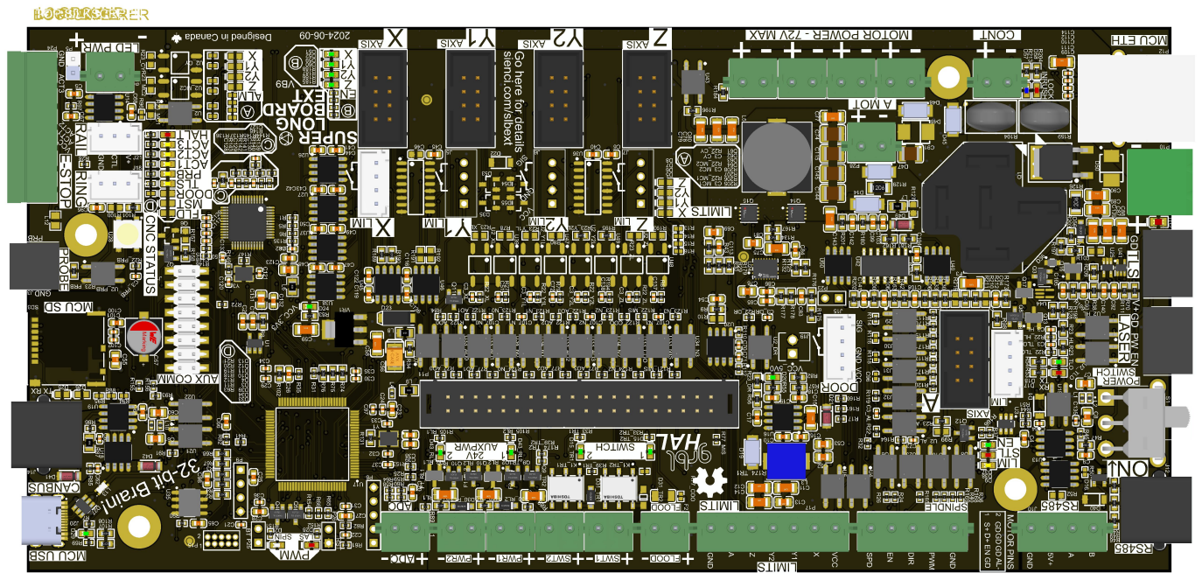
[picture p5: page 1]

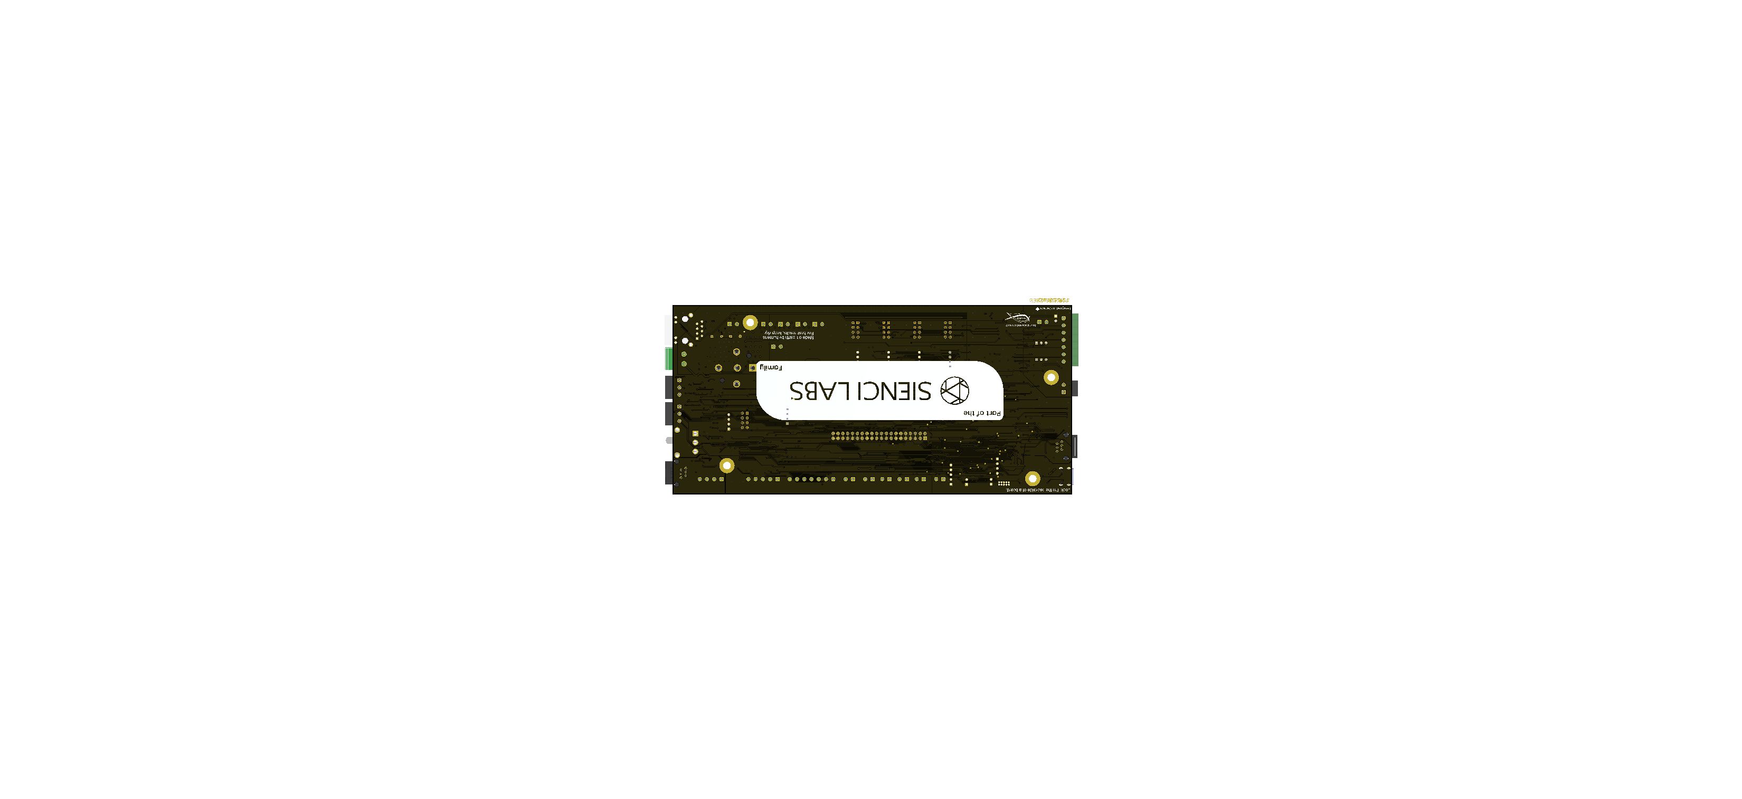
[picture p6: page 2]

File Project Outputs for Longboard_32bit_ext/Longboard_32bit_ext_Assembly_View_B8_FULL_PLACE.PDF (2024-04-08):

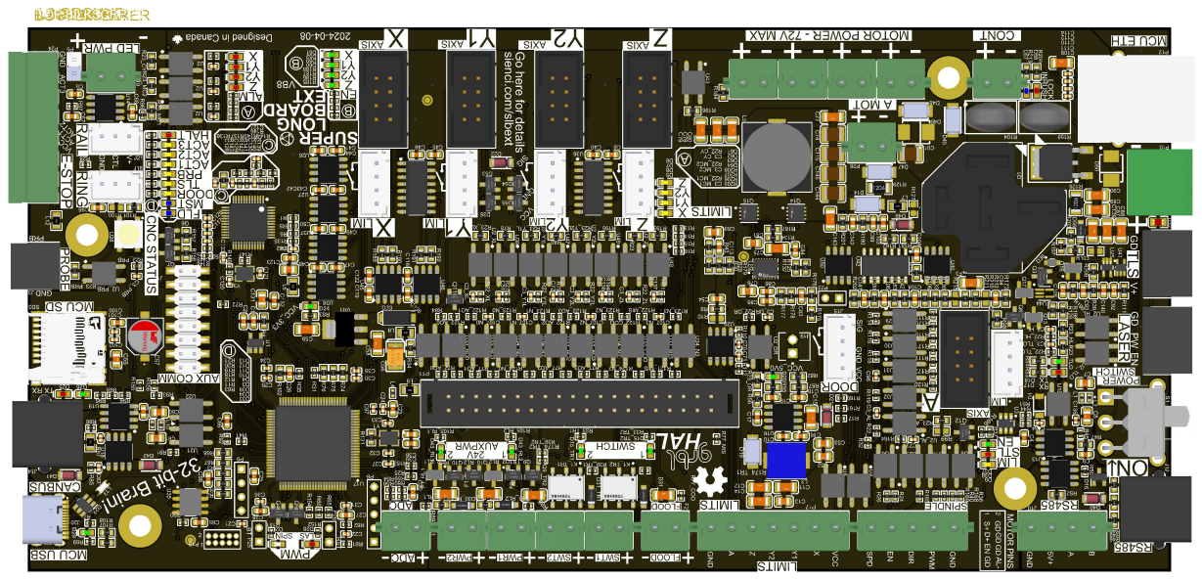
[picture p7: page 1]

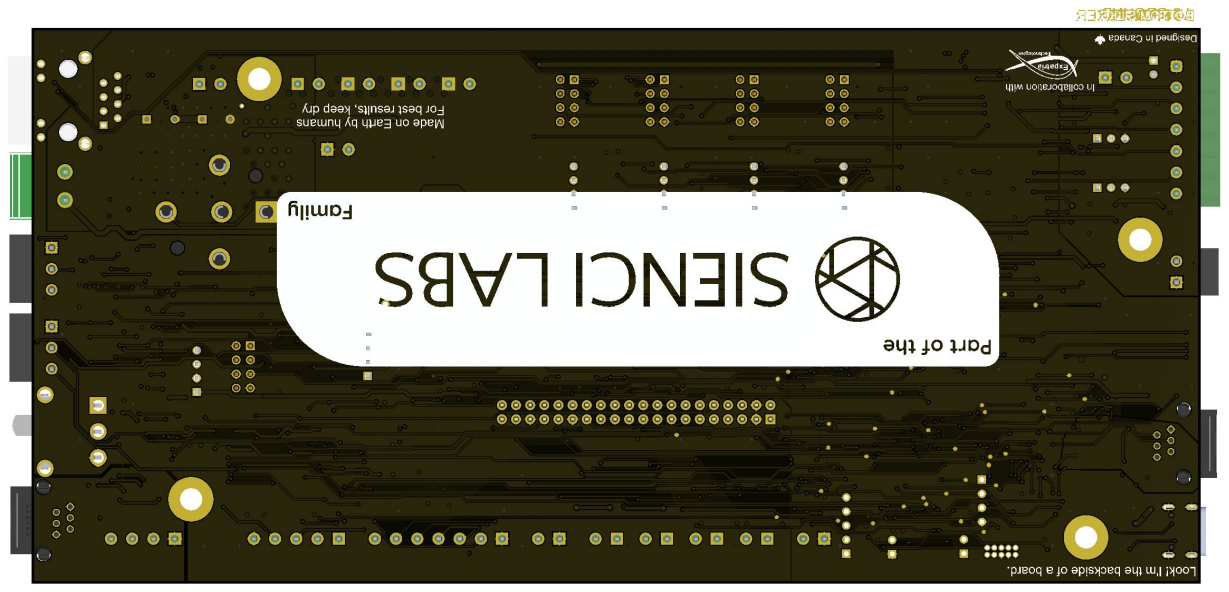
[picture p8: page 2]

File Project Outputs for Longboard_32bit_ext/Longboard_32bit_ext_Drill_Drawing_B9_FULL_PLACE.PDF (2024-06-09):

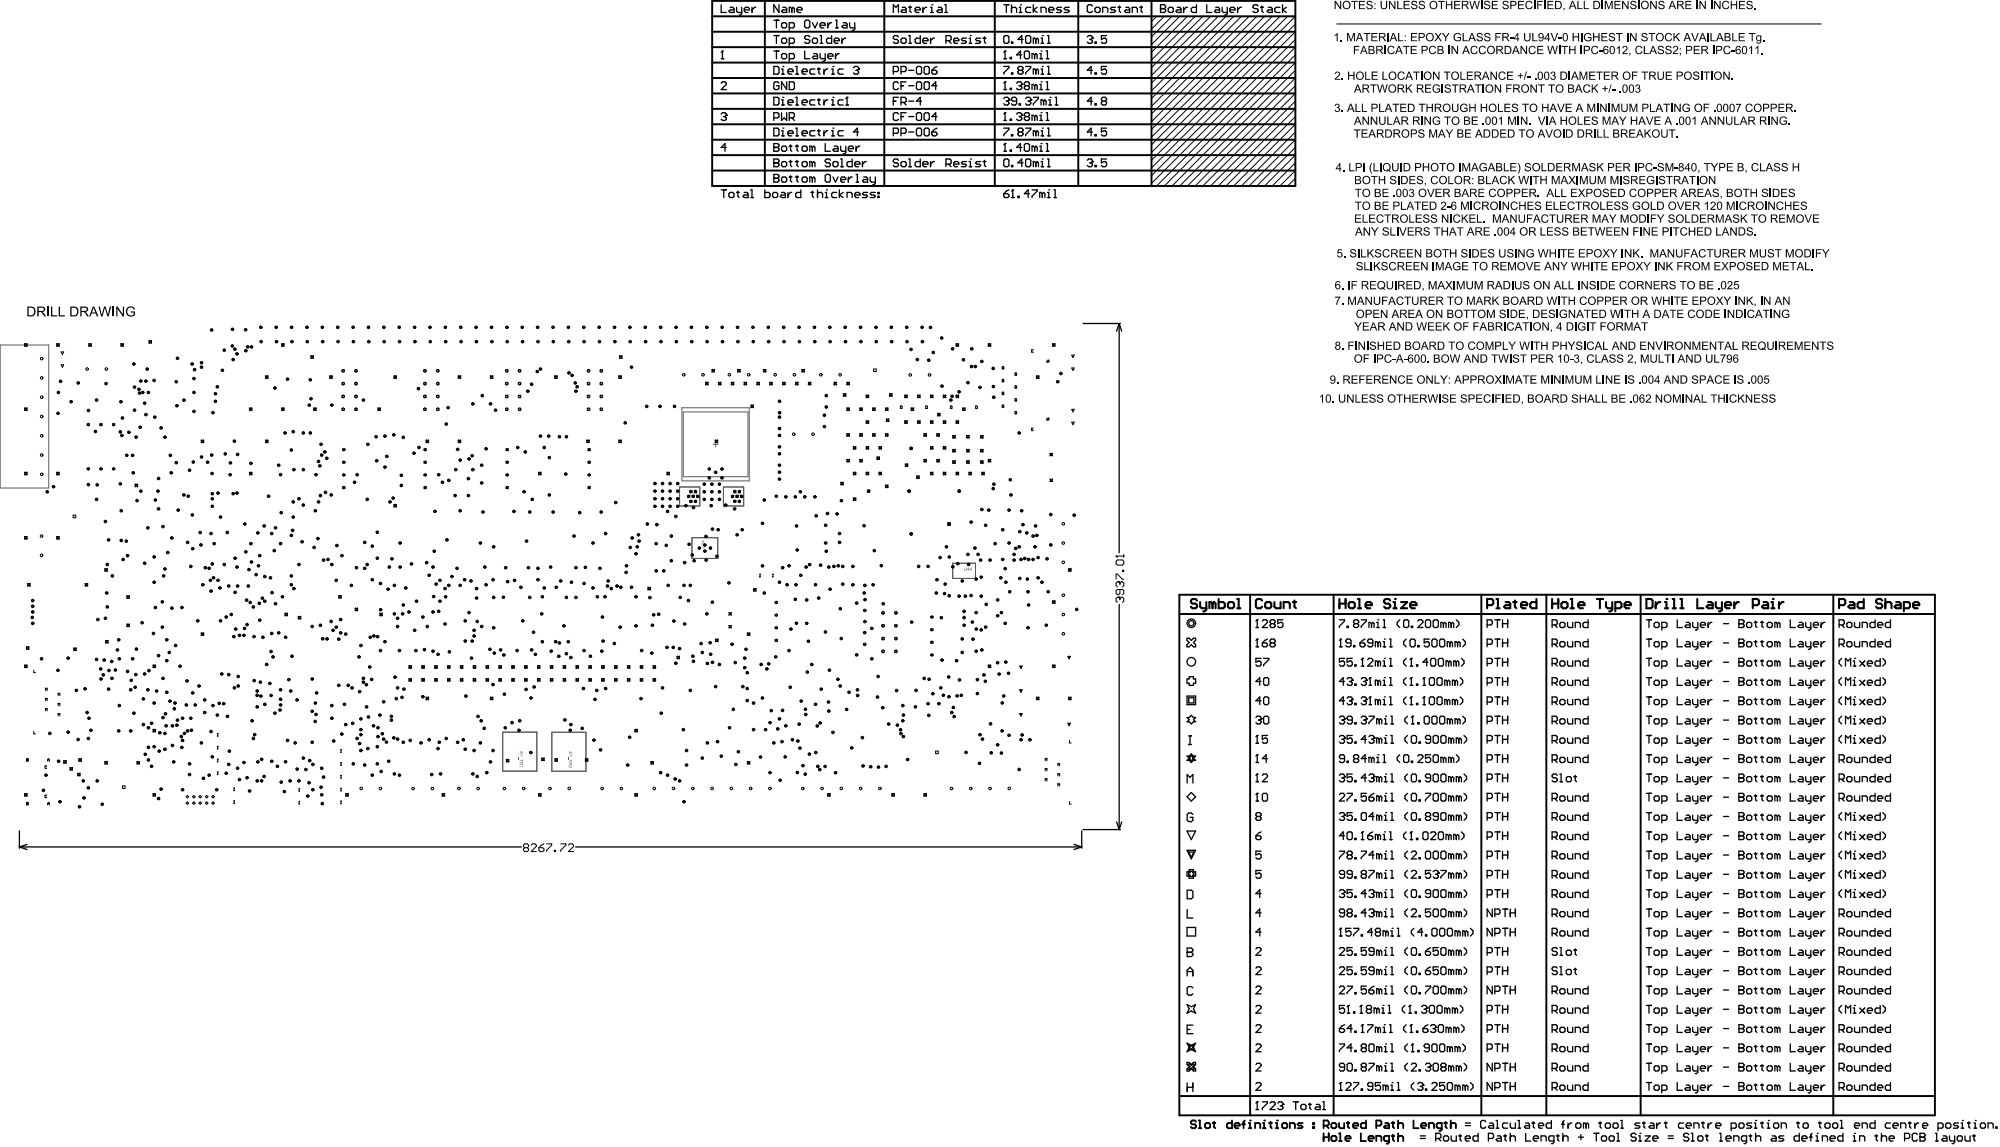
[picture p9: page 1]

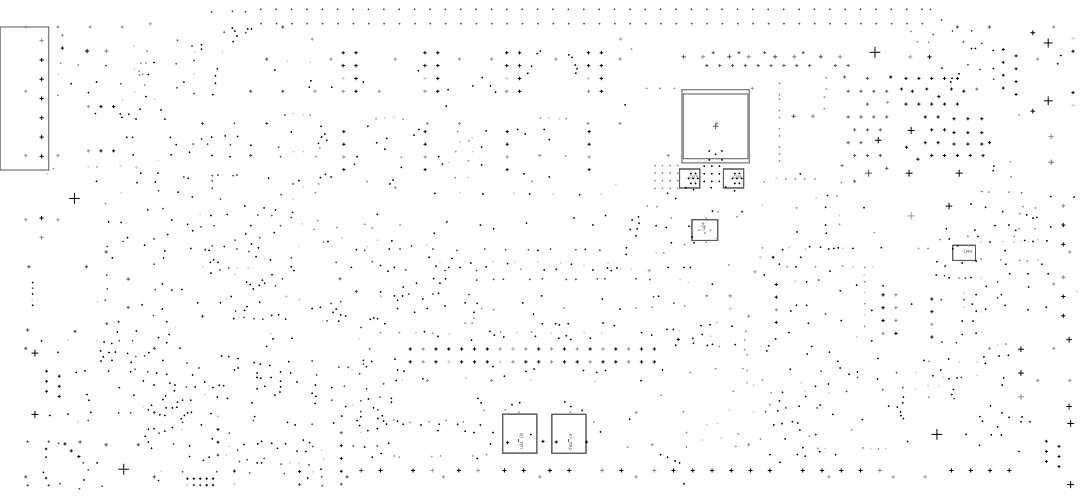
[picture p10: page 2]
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

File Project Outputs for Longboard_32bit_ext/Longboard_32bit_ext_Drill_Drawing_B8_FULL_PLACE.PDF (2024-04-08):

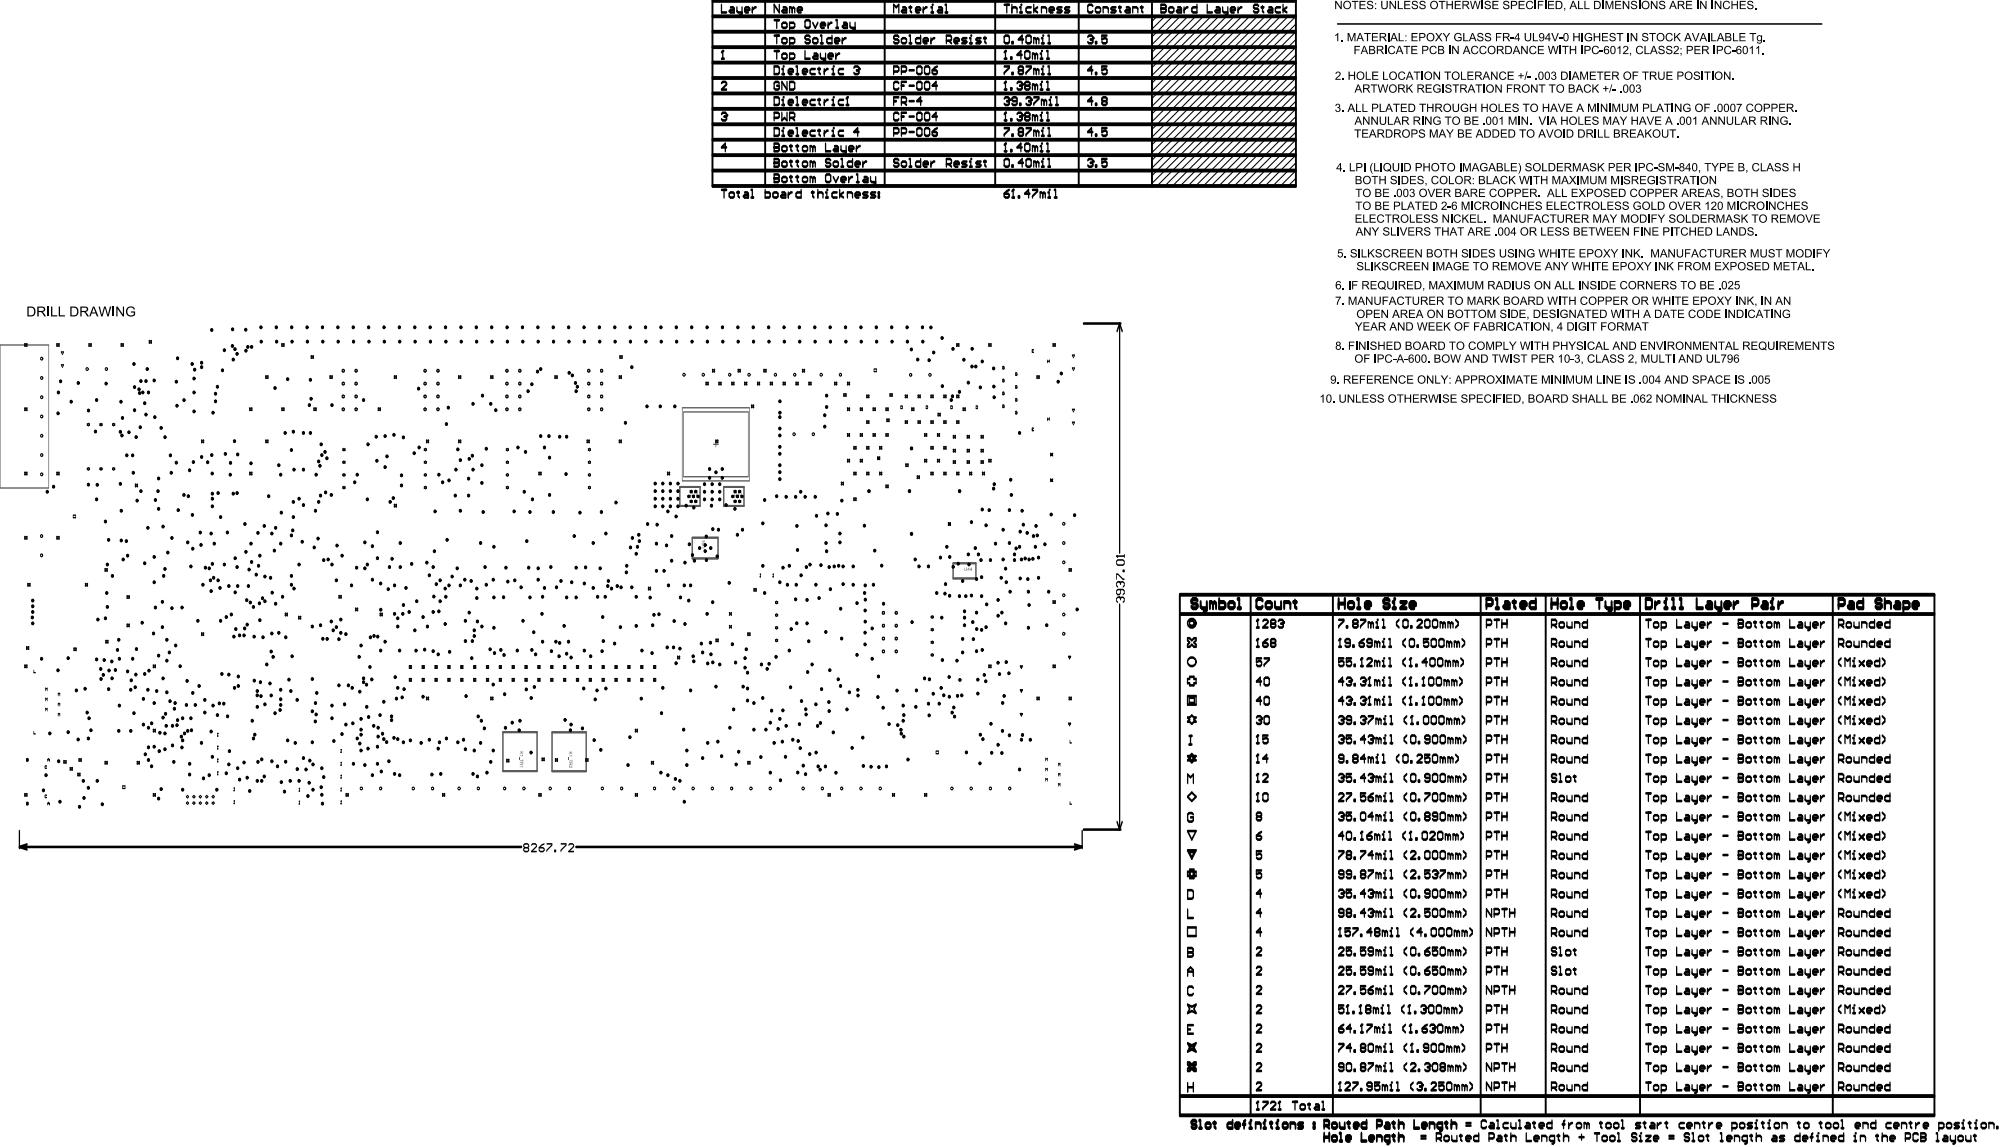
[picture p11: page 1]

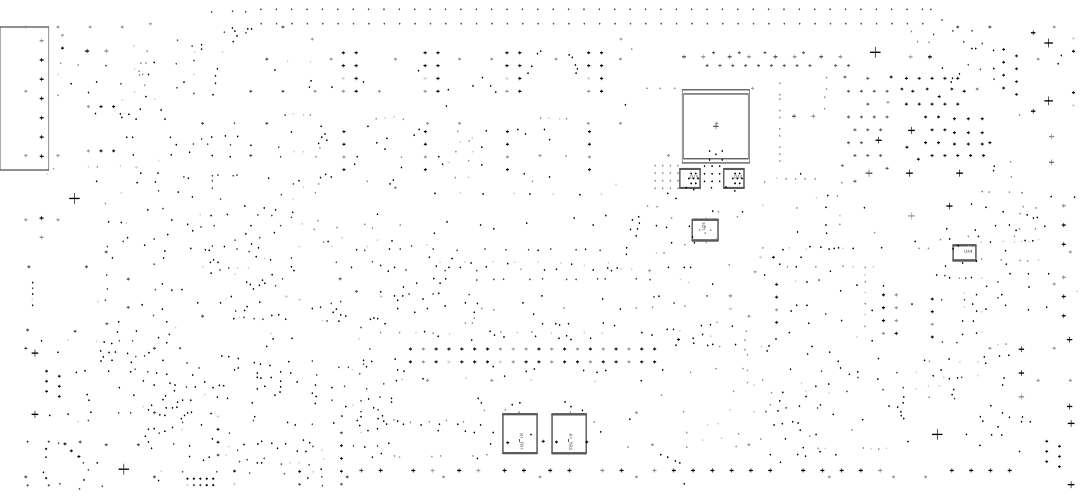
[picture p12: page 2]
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

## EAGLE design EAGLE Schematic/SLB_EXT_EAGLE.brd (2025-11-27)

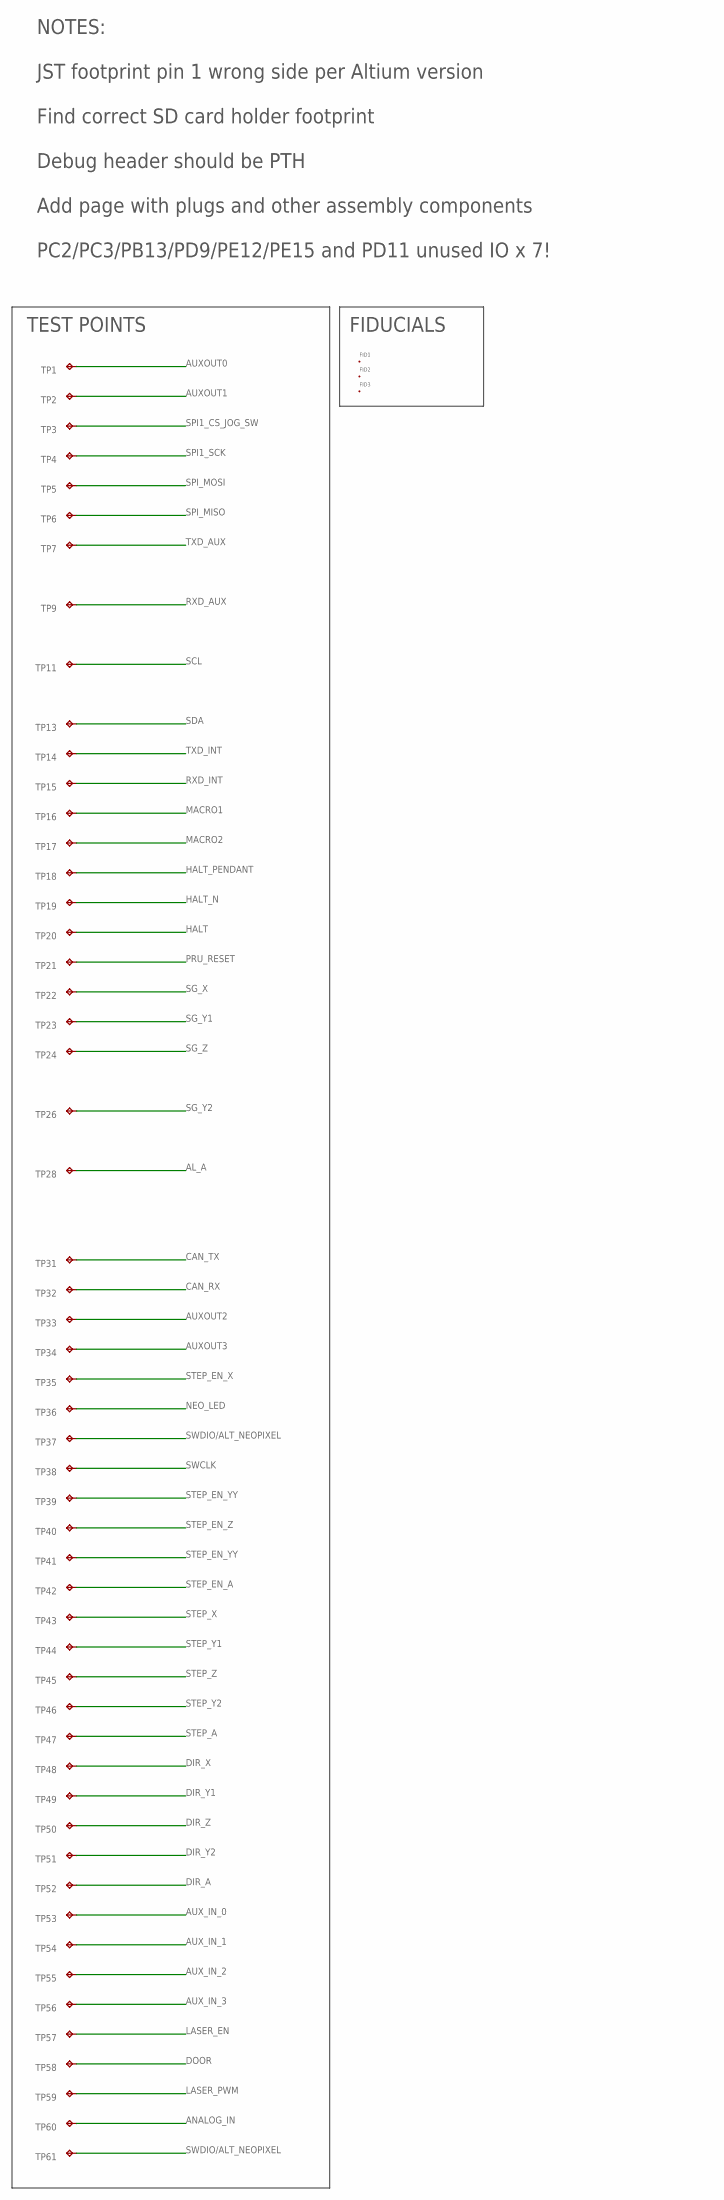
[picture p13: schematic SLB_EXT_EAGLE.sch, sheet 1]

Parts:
FID1, FID2, FID3: FID_40MIL_P; FID_040_P
TP1, TP2, TP3, TP4, TP5, TP6, TP7, TP9, TP11, TP13, TP14, TP15, TP16, TP17, TP18, TP19, TP20, TP21, TP22, TP23, TP24, TP26, TP28, TP31, TP32, TP33, TP34, TP35, TP36, TP37, TP38, TP39, TP40, TP41, TP42, TP43, TP44, TP45, TP46, TP47, TP48, TP49, TP50, TP51, TP52, TP53, TP54, TP55, TP56, TP57, TP58, TP59, TP60, TP61: TPB2,54; B2,54

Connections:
AL_A: TP28.TP; also elsewhere on the board
ANALOG_IN: TP60.TP; also elsewhere on the board
AUXOUT0: TP1.TP; also elsewhere on the board
AUXOUT1: TP2.TP; also elsewhere on the board
AUXOUT2: TP33.TP; also elsewhere on the board
AUXOUT3: TP34.TP; also elsewhere on the board
AUX_IN_0: TP53.TP; also elsewhere on the board
AUX_IN_1: TP54.TP; also elsewhere on the board
AUX_IN_2: TP55.TP; also elsewhere on the board
AUX_IN_3: TP56.TP; also elsewhere on the board
CAN_RX: TP32.TP; also elsewhere on the board
CAN_TX: TP31.TP; also elsewhere on the board
DIR_A: TP52.TP; also elsewhere on the board
DIR_X: TP48.TP; also elsewhere on the board
DIR_Y1: TP49.TP; also elsewhere on the board
DIR_Y2: TP51.TP; also elsewhere on the board
DIR_Z: TP50.TP; also elsewhere on the board
DOOR: TP58.TP; also elsewhere on the board
HALT: TP20.TP; also elsewhere on the board
HALT_N: TP19.TP; also elsewhere on the board
HALT_PENDANT: TP18.TP; also elsewhere on the board
LASER_EN: TP57.TP; also elsewhere on the board
LASER_PWM: TP59.TP; also elsewhere on the board
MACRO1: TP16.TP; also elsewhere on the board
MACRO2: TP17.TP; also elsewhere on the board
NEO_LED: TP36.TP; also elsewhere on the board
PRU_RESET: TP21.TP; also elsewhere on the board
RXD_AUX: TP9.TP; also elsewhere on the board
RXD_INT: TP15.TP; also elsewhere on the board
SCL: TP11.TP; also elsewhere on the board
SDA: TP13.TP; also elsewhere on the board
SG_X: TP22.TP; also elsewhere on the board
SG_Y1: TP23.TP; also elsewhere on the board
SG_Y2: TP26.TP; also elsewhere on the board
SG_Z: TP24.TP; also elsewhere on the board
SPI1_CS_JOG_SW: TP3.TP; also elsewhere on the board
SPI1_SCK: TP4.TP; also elsewhere on the board
SPI_MISO: TP6.TP; also elsewhere on the board
SPI_MOSI: TP5.TP; also elsewhere on the board
STEP_A: TP47.TP; also elsewhere on the board
STEP_EN_A: TP42.TP; also elsewhere on the board
STEP_EN_X: TP35.TP; also elsewhere on the board
STEP_EN_YY: TP39.TP, TP41.TP; also elsewhere on the board
STEP_EN_Z: TP40.TP; also elsewhere on the board
STEP_X: TP43.TP; also elsewhere on the board
STEP_Y1: TP44.TP; also elsewhere on the board
STEP_Y2: TP46.TP; also elsewhere on the board
STEP_Z: TP45.TP; also elsewhere on the board
SWCLK: TP38.TP; also elsewhere on the board
SWDIO/ALT_NEOPIXEL: TP37.TP, TP61.TP; also elsewhere on the board
TXD_AUX: TP7.TP; also elsewhere on the board
TXD_INT: TP14.TP; also elsewhere on the board

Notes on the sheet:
NOTES: JST footprint pin 1 wrong side per Altium version Find correct SD card holder footprint Debug header should be PTH Add page with plugs and other assembly components PC2/PC3/PB13/PD9/PE12/PE15 and PD11 unused IO x 7!
TEST POINTS
FIDUCIALS

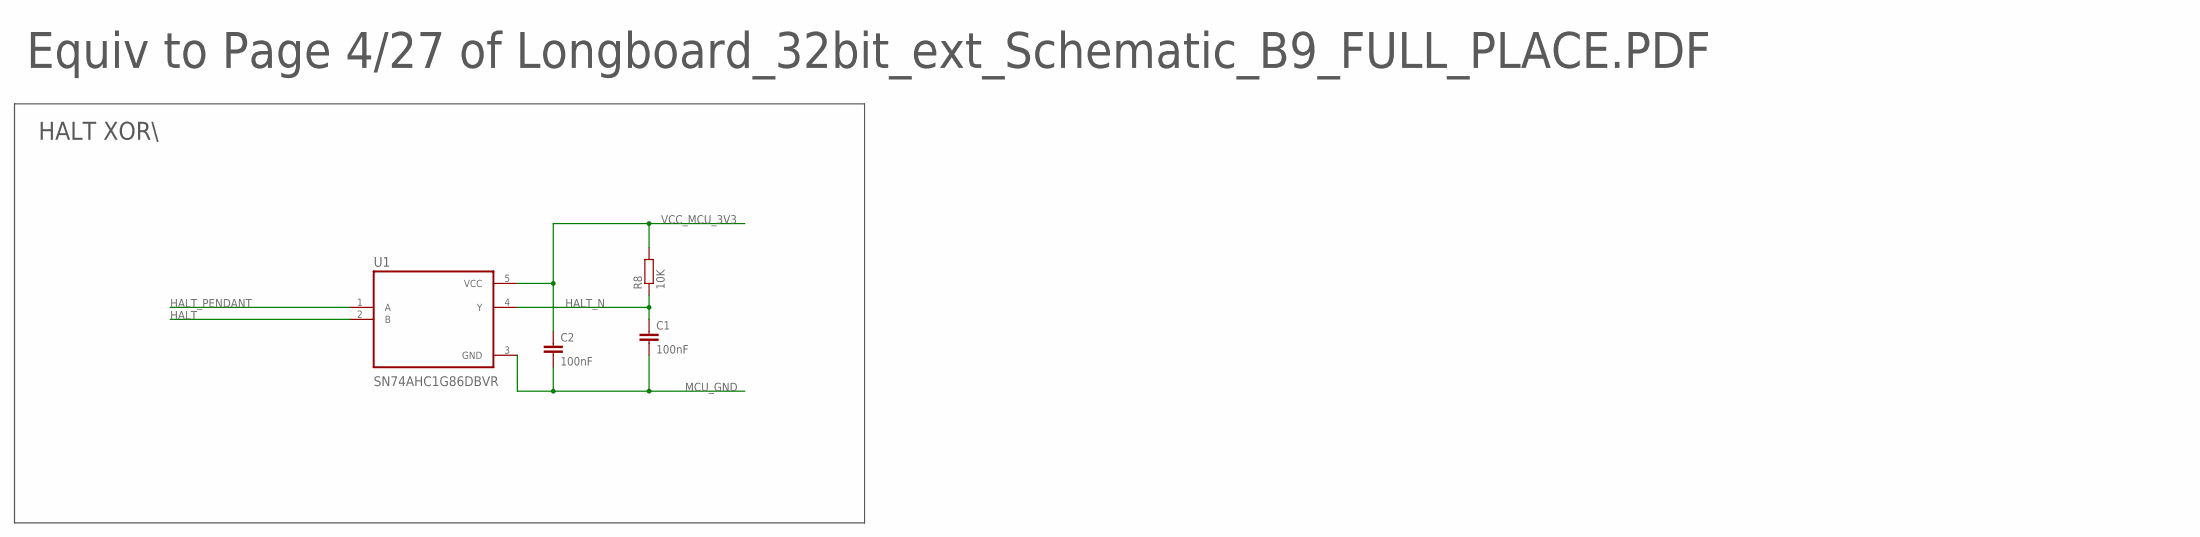
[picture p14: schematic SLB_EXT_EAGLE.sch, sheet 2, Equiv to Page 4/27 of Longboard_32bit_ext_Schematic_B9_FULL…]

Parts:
C1, C2: 100nF; C0402
R8: 10K; R0402
U1: SN74AHC1G86DBVR; SOT95P280X145-5N

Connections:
HALT: U1.2 (B); also elsewhere on the board
HALT_N: C1.1, R8.1, U1.4 (Y); also elsewhere on the board
HALT_PENDANT: U1.1 (A); also elsewhere on the board
MCU_GND: C1.2, C2.2, U1.3 (GND); also elsewhere on the board
VCC_MCU_3V3: C2.1, R8.2, U1.5 (VCC); also elsewhere on the board

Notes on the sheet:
Equiv to Page 4/27 of Longboard_32bit_ext_Schematic_B9_FULL_PLACE.PDF
HALT XOR\

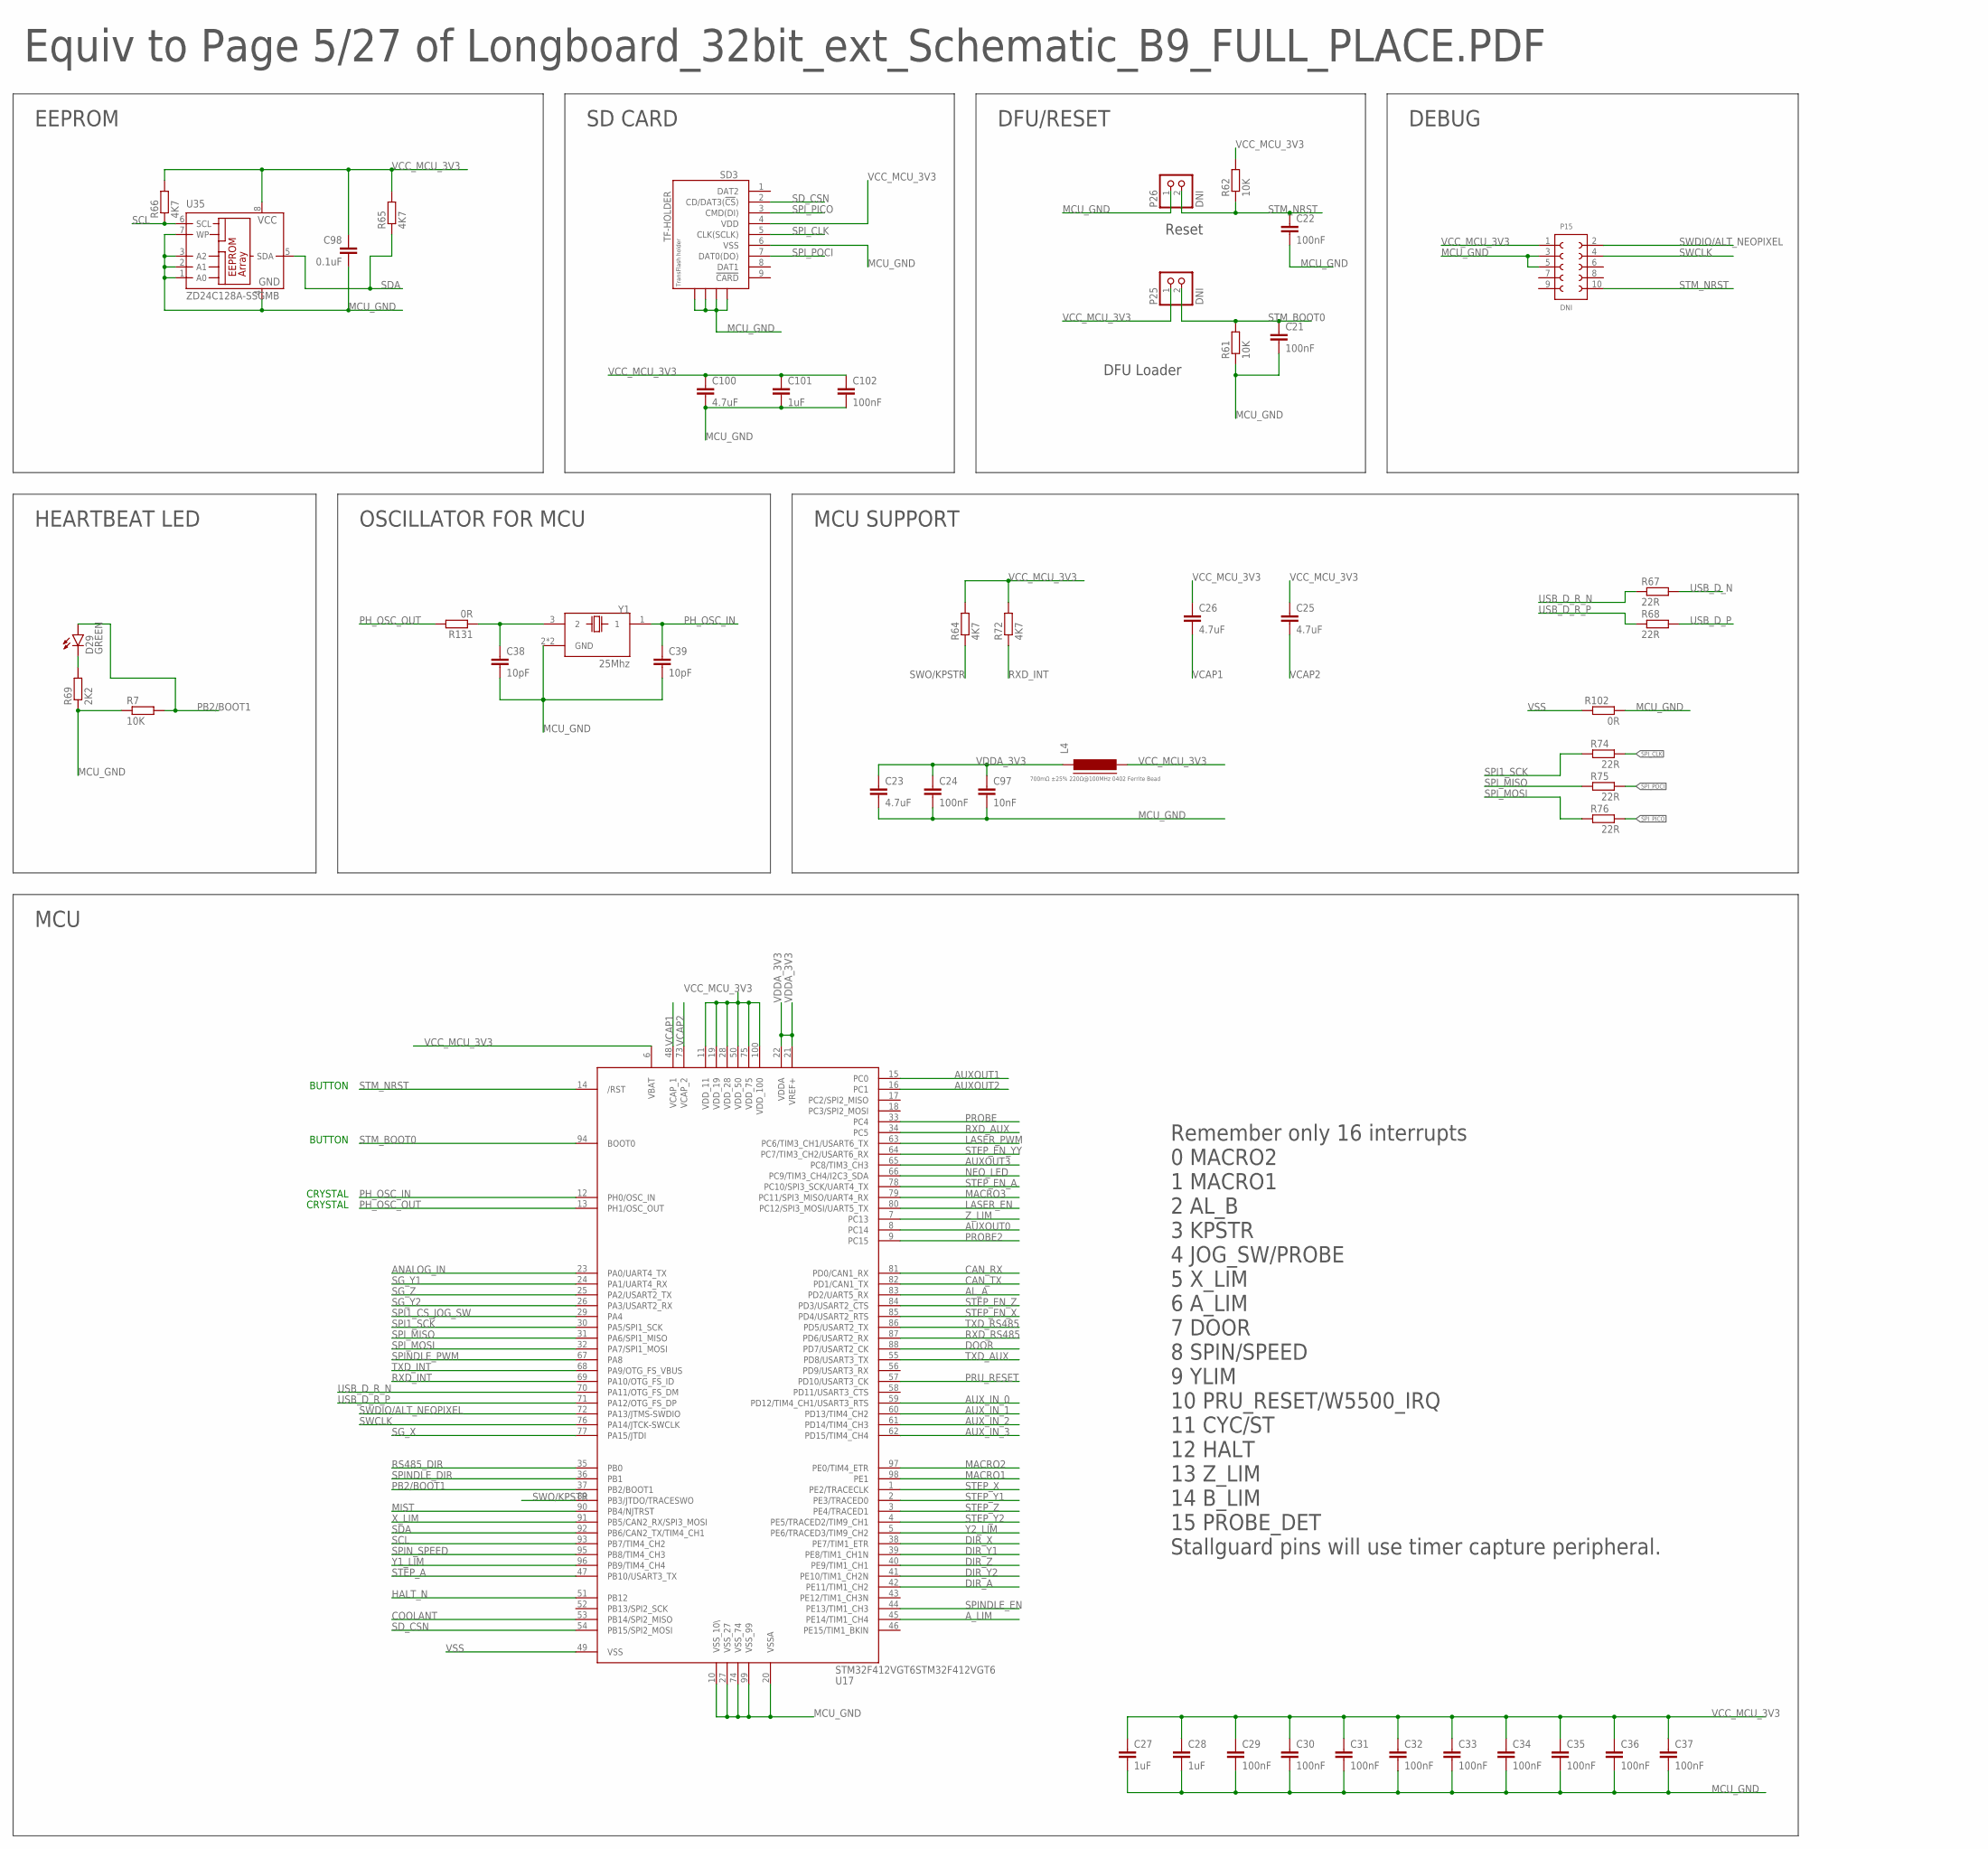
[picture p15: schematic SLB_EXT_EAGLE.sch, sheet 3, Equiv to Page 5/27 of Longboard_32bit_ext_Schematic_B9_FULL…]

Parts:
C21, C22, C24, C29, C30, C31, C32, C33, C34, C35, C36, C37, C102: 100nF; C0402
C23, C25, C26, C100: 4.7uF; C0603K
C27: 1uF; C0603
C28: 1uF; C0603K
C38, C39: 10pF; C0603K
C97: 10nF; C0402
C98: 0.1uF; 0805
C101: 1uF; C0402
D29: GREEN; CHIP-LED0603
L4: 700mΩ ±25% 220Ω@100MHz 0402 Ferrite Bead; FB402
P15: DNI; 621X1021021
P25, P26: DNI; 1X02
R7, R61, R62: 10K; R0402
R64, R65, R66, R72: 4K7; R0402
R67, R68, R74, R75, R76: 22R; R0603
R69: 2K2; R0402
R102, R131: 0R; R0603
SD3: TF-HOLDER; TF-PULL
U17: STM32F412VGT6STM32F412VGT6; LQFP100
U35: ZD24C128A-SSGMB; SO-08M
Y1: 25Mhz; XTAL_TSX-3225_16.0000MF18X-AC3

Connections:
AL_A: U17.83 (PD2/UART5_RX); also elsewhere on the board
ANALOG_IN: U17.23 (PA0/UART4_TX); also elsewhere on the board
AUXOUT0: U17.8 (PC14); also elsewhere on the board
AUXOUT1: U17.15 (PC0); also elsewhere on the board
AUXOUT2: U17.16 (PC1); also elsewhere on the board
AUXOUT3: U17.65 (PC8/TIM3_CH3); also elsewhere on the board
AUX_IN_0: U17.59 (PD12/TIM4_CH1/USART3_RTS); also elsewhere on the board
AUX_IN_1: U17.60 (PD13/TIM4_CH2); also elsewhere on the board
AUX_IN_2: U17.61 (PD14/TIM4_CH3); also elsewhere on the board
AUX_IN_3: U17.62 (PD15/TIM4_CH4); also elsewhere on the board
A_LIM: U17.45 (PE14/TIM1_CH4); also elsewhere on the board
CAN_RX: U17.81 (PD0/CAN1_RX); also elsewhere on the board
CAN_TX: U17.82 (PD1/CAN1_TX); also elsewhere on the board
COOLANT: U17.53 (PB14/SPI2_MISO); also elsewhere on the board
DIR_A: U17.42 (PE11/TIM1_CH2); also elsewhere on the board
DIR_X: U17.38 (PE7/TIM1_ETR); also elsewhere on the board
DIR_Y1: U17.39 (PE8/TIM1_CH1N); also elsewhere on the board
DIR_Y2: U17.41 (PE10/TIM1_CH2N); also elsewhere on the board
DIR_Z: U17.40 (PE9/TIM1_CH1); also elsewhere on the board
DOOR: U17.88 (PD7/USART2_CK); also elsewhere on the board
HALT_N: U17.51 (PB12); also elsewhere on the board
LASER_EN: U17.80 (PC12/SPI3_MOSI/UART5_TX); also elsewhere on the board
LASER_PWM: U17.63 (PC6/TIM3_CH1/USART6_TX); also elsewhere on the board
MACRO1: U17.98 (PE1); also elsewhere on the board
MACRO2: U17.97 (PE0/TIM4_ETR); also elsewhere on the board
MACRO3: U17.79 (PC11/SPI3_MISO/UART4_RX); also elsewhere on the board
MCU_GND: C21.2, C22.2, C23.2, C24.2, C27.2, C28.2, C29.2, C30.2, C31.2, C32.2, C33.2, C34.2, C35.2, C36.2, C37.2, C38.2, C39.2, C97.2, C98.2, C100.2, C101.2, C102.2, P15.3 (2), P15.5 (3), P26.1, R7.1, R61.1, R69.1, R102.1, SD3.6 (VSS), SD3.S1, SD3.S2, SD3.S3, SD3.S4, U17.10 (VSS_10\), U17.20 (VSSA), U17.27 (VSS_27), U17.74 (VSS_74), U17.99 (VSS_99), U35.1 (A0), U35.2 (A1), U35.3 (A2), U35.4 (GND), U35.7 (WP), Y1.2 (GND), Y1.4 (GND); also elsewhere on the board
MIST: U17.90 (PB4/NJTRST); also elsewhere on the board
unnamed: C38.1, R131.1, Y1.3 (2)
unnamed: D29.C, R69.2
NEO_LED: U17.66 (PC9/TIM3_CH4/I2C3_SDA); also elsewhere on the board
PB2/BOOT1: D29.A, R7.2, U17.37 (PB2/BOOT1)
PH_OSC_IN: C39.1, U17.12 (PH0/OSC_IN), Y1.1
PH_OSC_OUT: R131.2, U17.13 (PH1/OSC_OUT)
PROBE: U17.33 (PC4); also elsewhere on the board
PROBE2: U17.9 (PC15); also elsewhere on the board
PRU_RESET: U17.57 (PD10/USART3_CK); also elsewhere on the board
RS485_DIR: U17.35 (PB0); also elsewhere on the board
RXD_AUX: U17.34 (PC5); also elsewhere on the board
RXD_INT: R72.1, U17.69 (PA10/OTG_FS_ID); also elsewhere on the board
RXD_RS485: U17.87 (PD6/USART2_RX); also elsewhere on the board
SCL: R66.1, U17.93 (PB7/TIM4_CH2), U35.6 (SCL); also elsewhere on the board
SDA: R65.1, U17.92 (PB6/CAN2_TX/TIM4_CH1), U35.5 (SDA); also elsewhere on the board
SD_CSN: SD3.2 (CD/DAT3(!CS!)), U17.54 (PB15/SPI2_MOSI)
SG_X: U17.77 (PA15/JTDI); also elsewhere on the board
SG_Y1: U17.24 (PA1/UART4_RX); also elsewhere on the board
SG_Y2: U17.26 (PA3/USART2_RX); also elsewhere on the board
SG_Z: U17.25 (PA2/USART2_TX); also elsewhere on the board
SPI1_CS_JOG_SW: U17.29 (PA4); also elsewhere on the board
SPI1_SCK: R74.2, U17.30 (PA5/SPI1_SCK); also elsewhere on the board
SPINDLE_DIR: U17.36 (PB1); also elsewhere on the board
SPINDLE_EN: U17.44 (PE13/TIM1_CH3); also elsewhere on the board
SPINDLE_PWM: U17.67 (PA8); also elsewhere on the board
SPIN_SPEED: U17.95 (PB8/TIM4_CH3); also elsewhere on the board
SPI_CLK: R74.1, SD3.5 (CLK(SCLK)); also elsewhere on the board
SPI_MISO: R75.2, U17.31 (PA6/SPI1_MISO); also elsewhere on the board
SPI_MOSI: R76.2, U17.32 (PA7/SPI1_MOSI); also elsewhere on the board
SPI_PICO: R76.1, SD3.3 (CMD(DI)); also elsewhere on the board
SPI_POCI: R75.1, SD3.7 (DAT0(DO)); also elsewhere on the board
STEP_A: U17.47 (PB10/USART3_TX); also elsewhere on the board
STEP_EN_A: U17.78 (PC10/SPI3_SCK/UART4_TX); also elsewhere on the board
STEP_EN_X: U17.85 (PD4/USART2_RTS); also elsewhere on the board
STEP_EN_YY: U17.64 (PC7/TIM3_CH2/USART6_RX); also elsewhere on the board
STEP_EN_Z: U17.84 (PD3/USART2_CTS); also elsewhere on the board
STEP_X: U17.1 (PE2/TRACECLK); also elsewhere on the board
STEP_Y1: U17.2 (PE3/TRACED0); also elsewhere on the board
STEP_Y2: U17.4 (PE5/TRACED2/TIM9_CH1); also elsewhere on the board
STEP_Z: U17.3 (PE4/TRACED1); also elsewhere on the board
STM_BOOT0: C21.1, P25.2, R61.2, U17.94 (BOOT0); also elsewhere on the board
STM_NRST: C22.1, P15.10 (6), P26.2, R62.1, U17.14 (/RST); also elsewhere on the board
SWCLK: P15.4 (9), U17.76 (PA14/JTCK-SWCLK); also elsewhere on the board
SWDIO/ALT_NEOPIXEL: P15.2 (10), U17.72 (PA13/JTMS-SWDIO); also elsewhere on the board
SWO/KPSTR: R64.1, U17.89 (PB3/JTDO/TRACESWO)
TXD_AUX: U17.55 (PD8/USART3_TX); also elsewhere on the board
TXD_INT: U17.68 (PA9/OTG_FS_VBUS); also elsewhere on the board
TXD_RS485: U17.86 (PD5/USART2_TX); also elsewhere on the board
USB_D_N: R67.2; also elsewhere on the board
USB_D_P: R68.2; also elsewhere on the board
USB_D_R_N: R67.1, U17.70 (PA11/OTG_FS_DM)
USB_D_R_P: R68.1, U17.71 (PA12/OTG_FS_DP)
VCAP1: C26.2, U17.48 (VCAP_1)
VCAP2: C25.2, U17.73 (VCAP_2)
VCC_MCU_3V3: C25.1, C26.1, C27.1, C28.1, C29.1, C30.1, C31.1, C32.1, C33.1, C34.1, C35.1, C36.1, C37.1, C98.1, C100.1, C101.1, C102.1, L4.2, P15.1, P25.1, R62.2, R64.2, R65.2, R66.2, R72.2, SD3.4 (VDD), U17.6 (VBAT), U17.11 (VDD_11), U17.19 (VDD_19), U17.28 (VDD_28), U17.50 (VDD_50), U17.75 (VDD_75), U17.100 (VDD_100), U35.8 (VCC); also elsewhere on the board
VDDA_3V3: C23.1, C24.1, C97.1, L4.1, U17.21 (VREF+), U17.22 (VDDA)
VSS: R102.2, U17.49 (VSS)
X_LIM: U17.91 (PB5/CAN2_RX/SPI3_MOSI); also elsewhere on the board
Y1_LIM: U17.96 (PB9/TIM4_CH4); also elsewhere on the board
Y2_LIM: U17.5 (PE6/TRACED3/TIM9_CH2); also elsewhere on the board
Z_LIM: U17.7 (PC13); also elsewhere on the board

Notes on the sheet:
Reset
DFU Loader
CRYSTAL
BUTTON
Equiv to Page 5/27 of Longboard_32bit_ext_Schematic_B9_FULL_PLACE.PDF
EEPROM
SD CARD
DFU/RESET
DEBUG
HEARTBEAT LED
OSCILLATOR FOR MCU
MCU SUPPORT
MCU
Remember only 16 interrupts 0 MACRO2 1 MACRO1 2 AL_B 3 KPSTR 4 JOG_SW/PROBE 5 X_LIM 6 A_LIM 7 DOOR 8 SPIN/SPEED 9 YLIM 10 PRU_RESET/W5500_IRQ 11 CYC/ST 12 HALT 13 Z_LIM 14 B_LIM 15 PROBE_DET Stallguard pins will use timer capture peripheral.

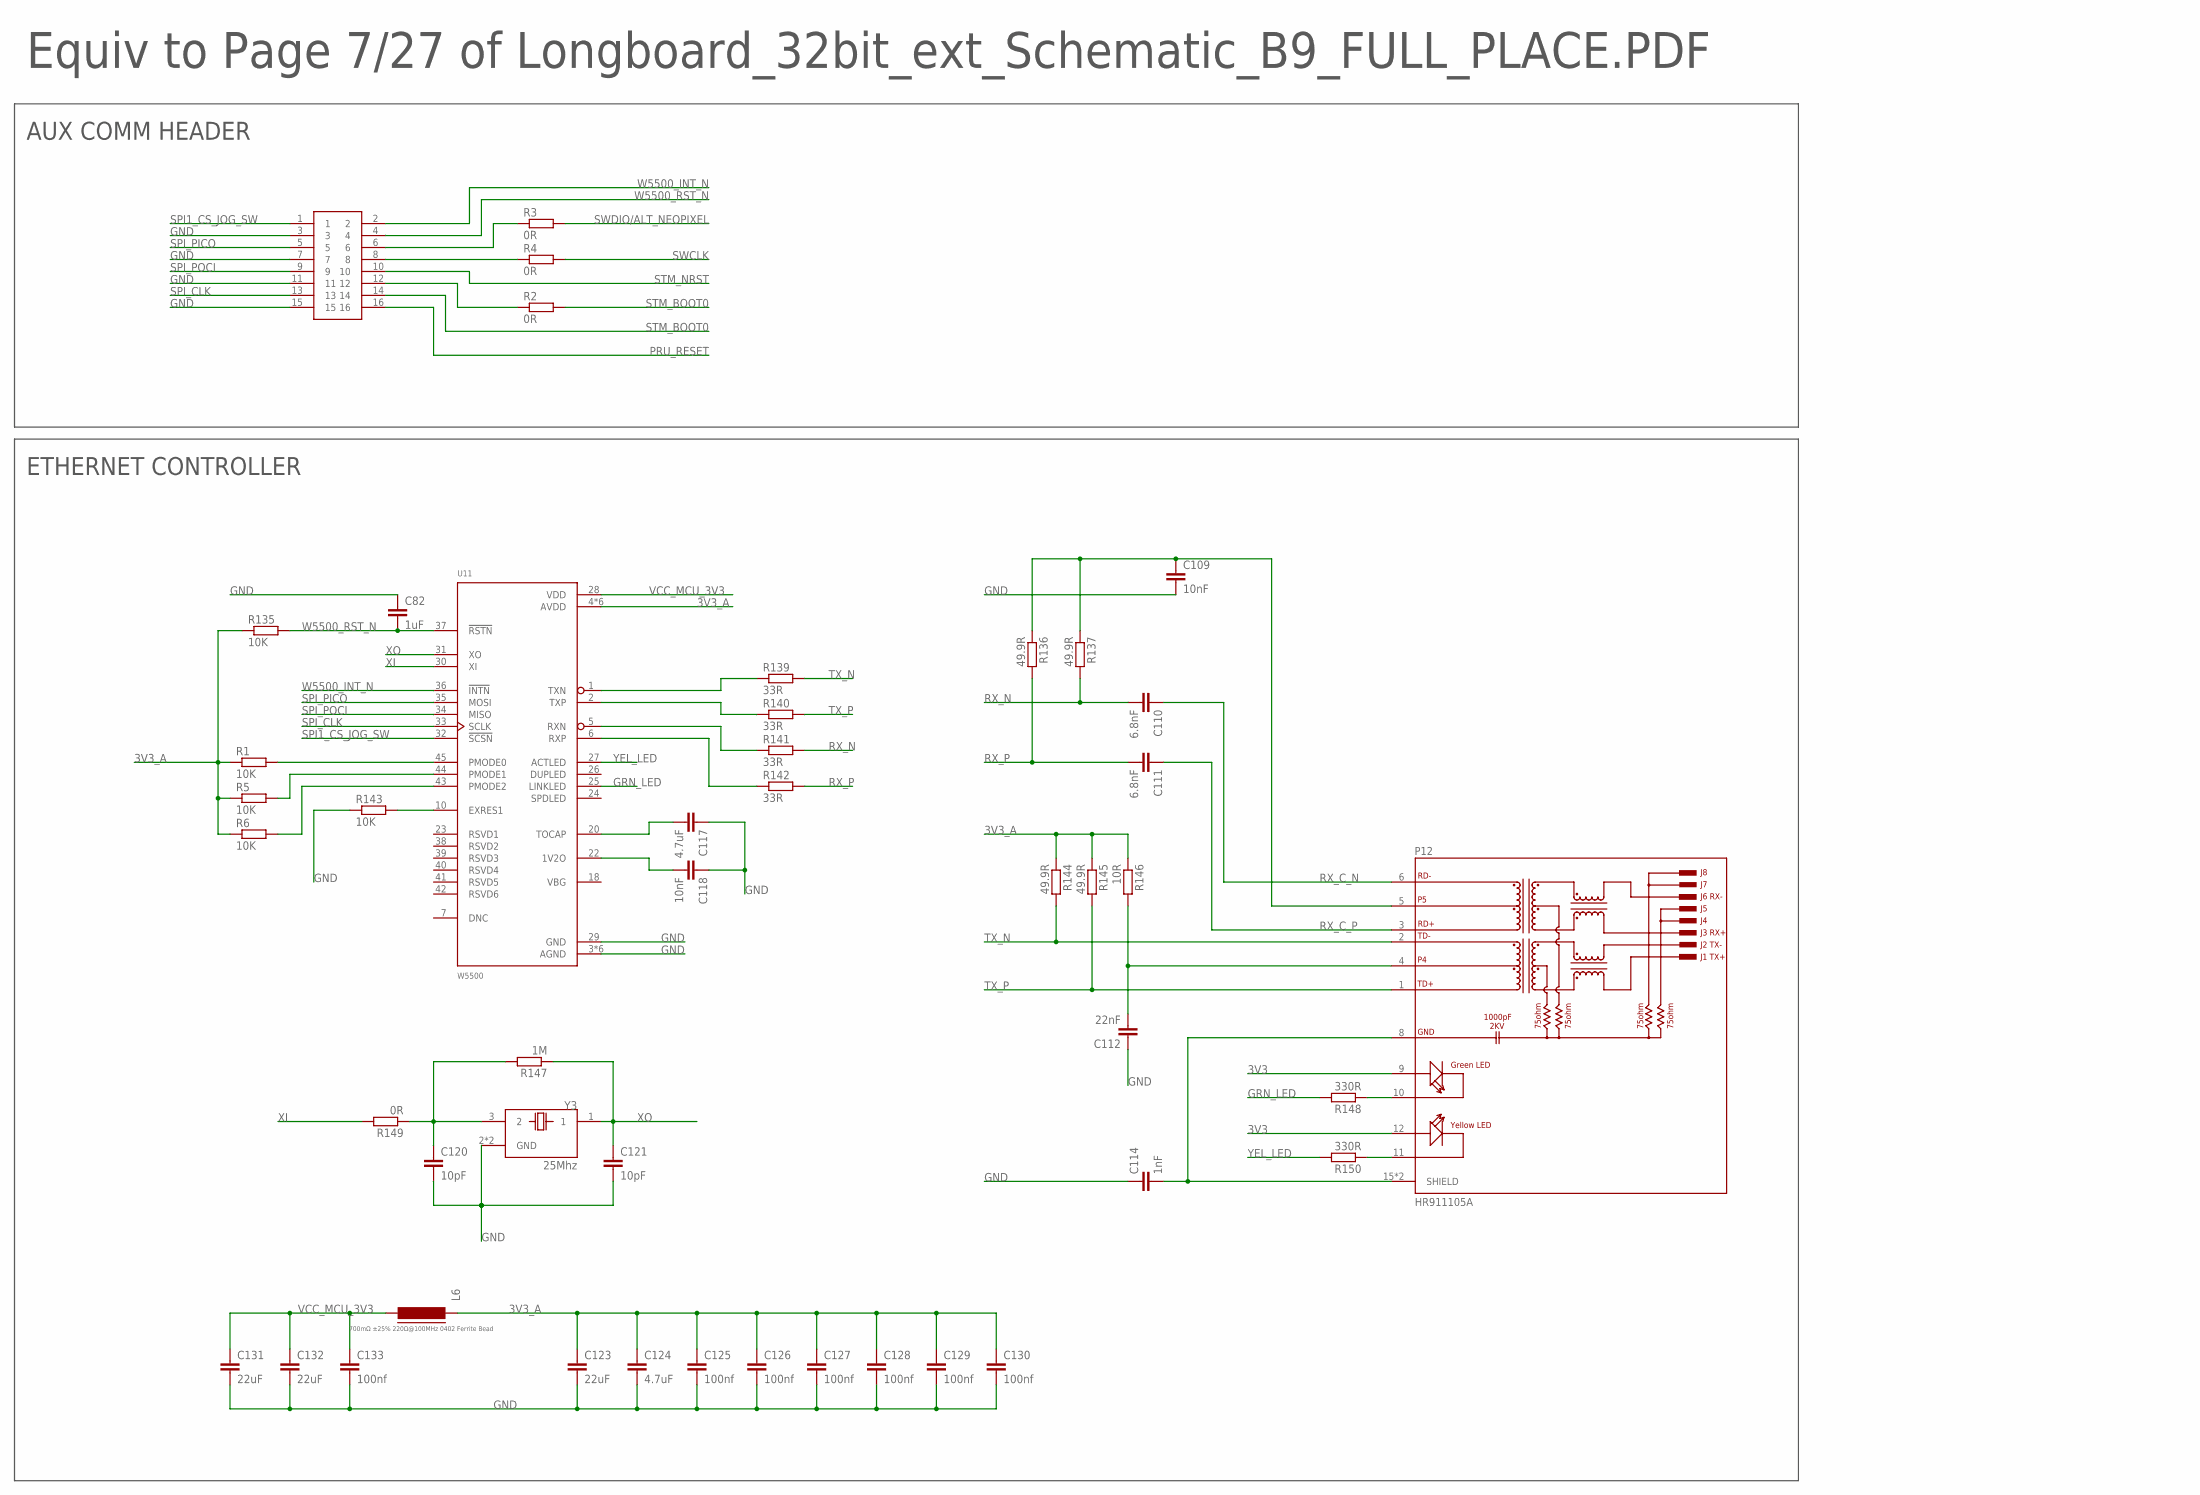
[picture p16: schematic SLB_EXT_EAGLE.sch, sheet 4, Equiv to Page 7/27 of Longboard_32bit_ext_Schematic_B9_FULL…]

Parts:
C82: 1uF; C0402
C109, C118: 10nF; C0402
C110, C111: 6.8nF; C0402
C112: 22nF; C0402
C114: 1nF; C1206
C117: 4.7uF; C0402
C120, C121: 10pF; C0402
C123, C131, C132: 22uF; C0603K
C124: 4.7uF; C0603K
C125, C126, C127, C129, C130, C133: 100nf; C0402
C128: 100nf; C0603K
J1: 16P_HEADER_SMD; 16_PIN_SMD_PIN_HEADER
L6: 700mΩ ±25% 220Ω@100MHz 0402 Ferrite Bead; FB402
P12: HR911105A; HANRUN_HR911105A
R1, R5, R6, R135: 10K; R0402
R2, R3, R4: 0R; R0603
R136, R137, R144, R145: 49.9R; R0402
R139, R140, R141, R142: 33R; R0402
R143: 10K; R0603
R146: 10R; R0402
R147: 1M; R0402
R148, R150: 330R; R0402
R149: 0R; R0402
U11: W5500; QFP50P900X900X160-48N
Y3: 25Mhz; XTAL_TSX-3225_16.0000MF18X-AC3

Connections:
3V3: P12.9 (GA), P12.12 (YA)
3V3_A: C123.1, C124.1, C125.1, C126.1, C127.1, C128.1, C129.1, C130.1, L6.1, R1.1, R5.1, R6.1, R135.1, R144.1, R145.1, R146.1, U11.4 (AVDD), U11.8 (AVDD), U11.11 (AVDD), U11.15 (AVDD), U11.17 (AVDD), U11.21 (AVDD)
GND: C82.1, C109.2, C112.1, C114.1, C117.1, C118.1, C120.2, C121.2, C123.2, C124.2, C125.2, C126.2, C127.2, C128.2, C129.2, C130.2, C131.2, C132.2, C133.2, J1.3, J1.7, J1.11, J1.15, R143.1, U11.3 (AGND), U11.9 (AGND), U11.14 (AGND), U11.16 (AGND), U11.19 (AGND), U11.29 (GND), U11.48 (AGND), Y3.2 (GND), Y3.4 (GND); also elsewhere on the board
GRN_LED: R148.2, U11.25 (LINKLED)
unnamed: P12.11 (YC), R150.1
unnamed: P12.10 (GC), R148.1
unnamed: C114.2, P12.8 (GND), P12.15 (SHIELD), P12.16 (SHIELD)
unnamed: C120.1, R147.2, R149.1, Y3.3 (2)
unnamed: C112.2, P12.4, R146.2
unnamed: R139.1, U11.1 (TXN)
unnamed: R140.1, U11.2 (TXP)
unnamed: C109.1, P12.5, R136.1, R137.1
unnamed: R141.1, U11.5 (RXN)
unnamed: R142.1, U11.6 (RXP)
unnamed: R143.2, U11.10 (EXRES1)
unnamed: C117.2, U11.20 (TOCAP)
unnamed: C118.2, U11.22 (1V2O)
unnamed: R6.2, U11.43 (PMODE2)
unnamed: R5.2, U11.44 (PMODE1)
unnamed: R1.2, U11.45 (PMODE0)
unnamed: J1.6, R3.1
unnamed: J1.8, R4.1
unnamed: J1.12, R2.1
PRU_RESET: J1.16; also elsewhere on the board
RX_C_N: C110.1, P12.6 (RD-)
RX_C_P: C111.1, P12.3 (RD+)
RX_N: C110.2, R137.2, R141.2
RX_P: C111.2, R136.2, R142.2
SPI1_CS_JOG_SW: J1.1, U11.32 (!SCSN); also elsewhere on the board
SPI_CLK: J1.13, U11.33 (SCLK); also elsewhere on the board
SPI_PICO: J1.5, U11.35 (MOSI); also elsewhere on the board
SPI_POCI: J1.9, U11.34 (MISO); also elsewhere on the board
STM_BOOT0: J1.14, R2.2; also elsewhere on the board
STM_NRST: J1.10; also elsewhere on the board
SWCLK: R4.2; also elsewhere on the board
SWDIO/ALT_NEOPIXEL: R3.2; also elsewhere on the board
TX_N: P12.2 (TD-), R139.2, R144.2
TX_P: P12.1 (TD+), R140.2, R145.2
VCC_MCU_3V3: C131.1, C132.1, C133.1, L6.2, U11.28 (VDD); also elsewhere on the board
W5500_INT_N: J1.2, U11.36 (!INTN)
W5500_RST_N: C82.2, J1.4, R135.2, U11.37 (!RSTN)
XI: R149.2, U11.30 (XI)
XO: C121.1, R147.1, U11.31 (XO), Y3.1
YEL_LED: R150.2, U11.27 (ACTLED)

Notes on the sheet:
Equiv to Page 7/27 of Longboard_32bit_ext_Schematic_B9_FULL_PLACE.PDF
ETHERNET CONTROLLER
AUX COMM HEADER

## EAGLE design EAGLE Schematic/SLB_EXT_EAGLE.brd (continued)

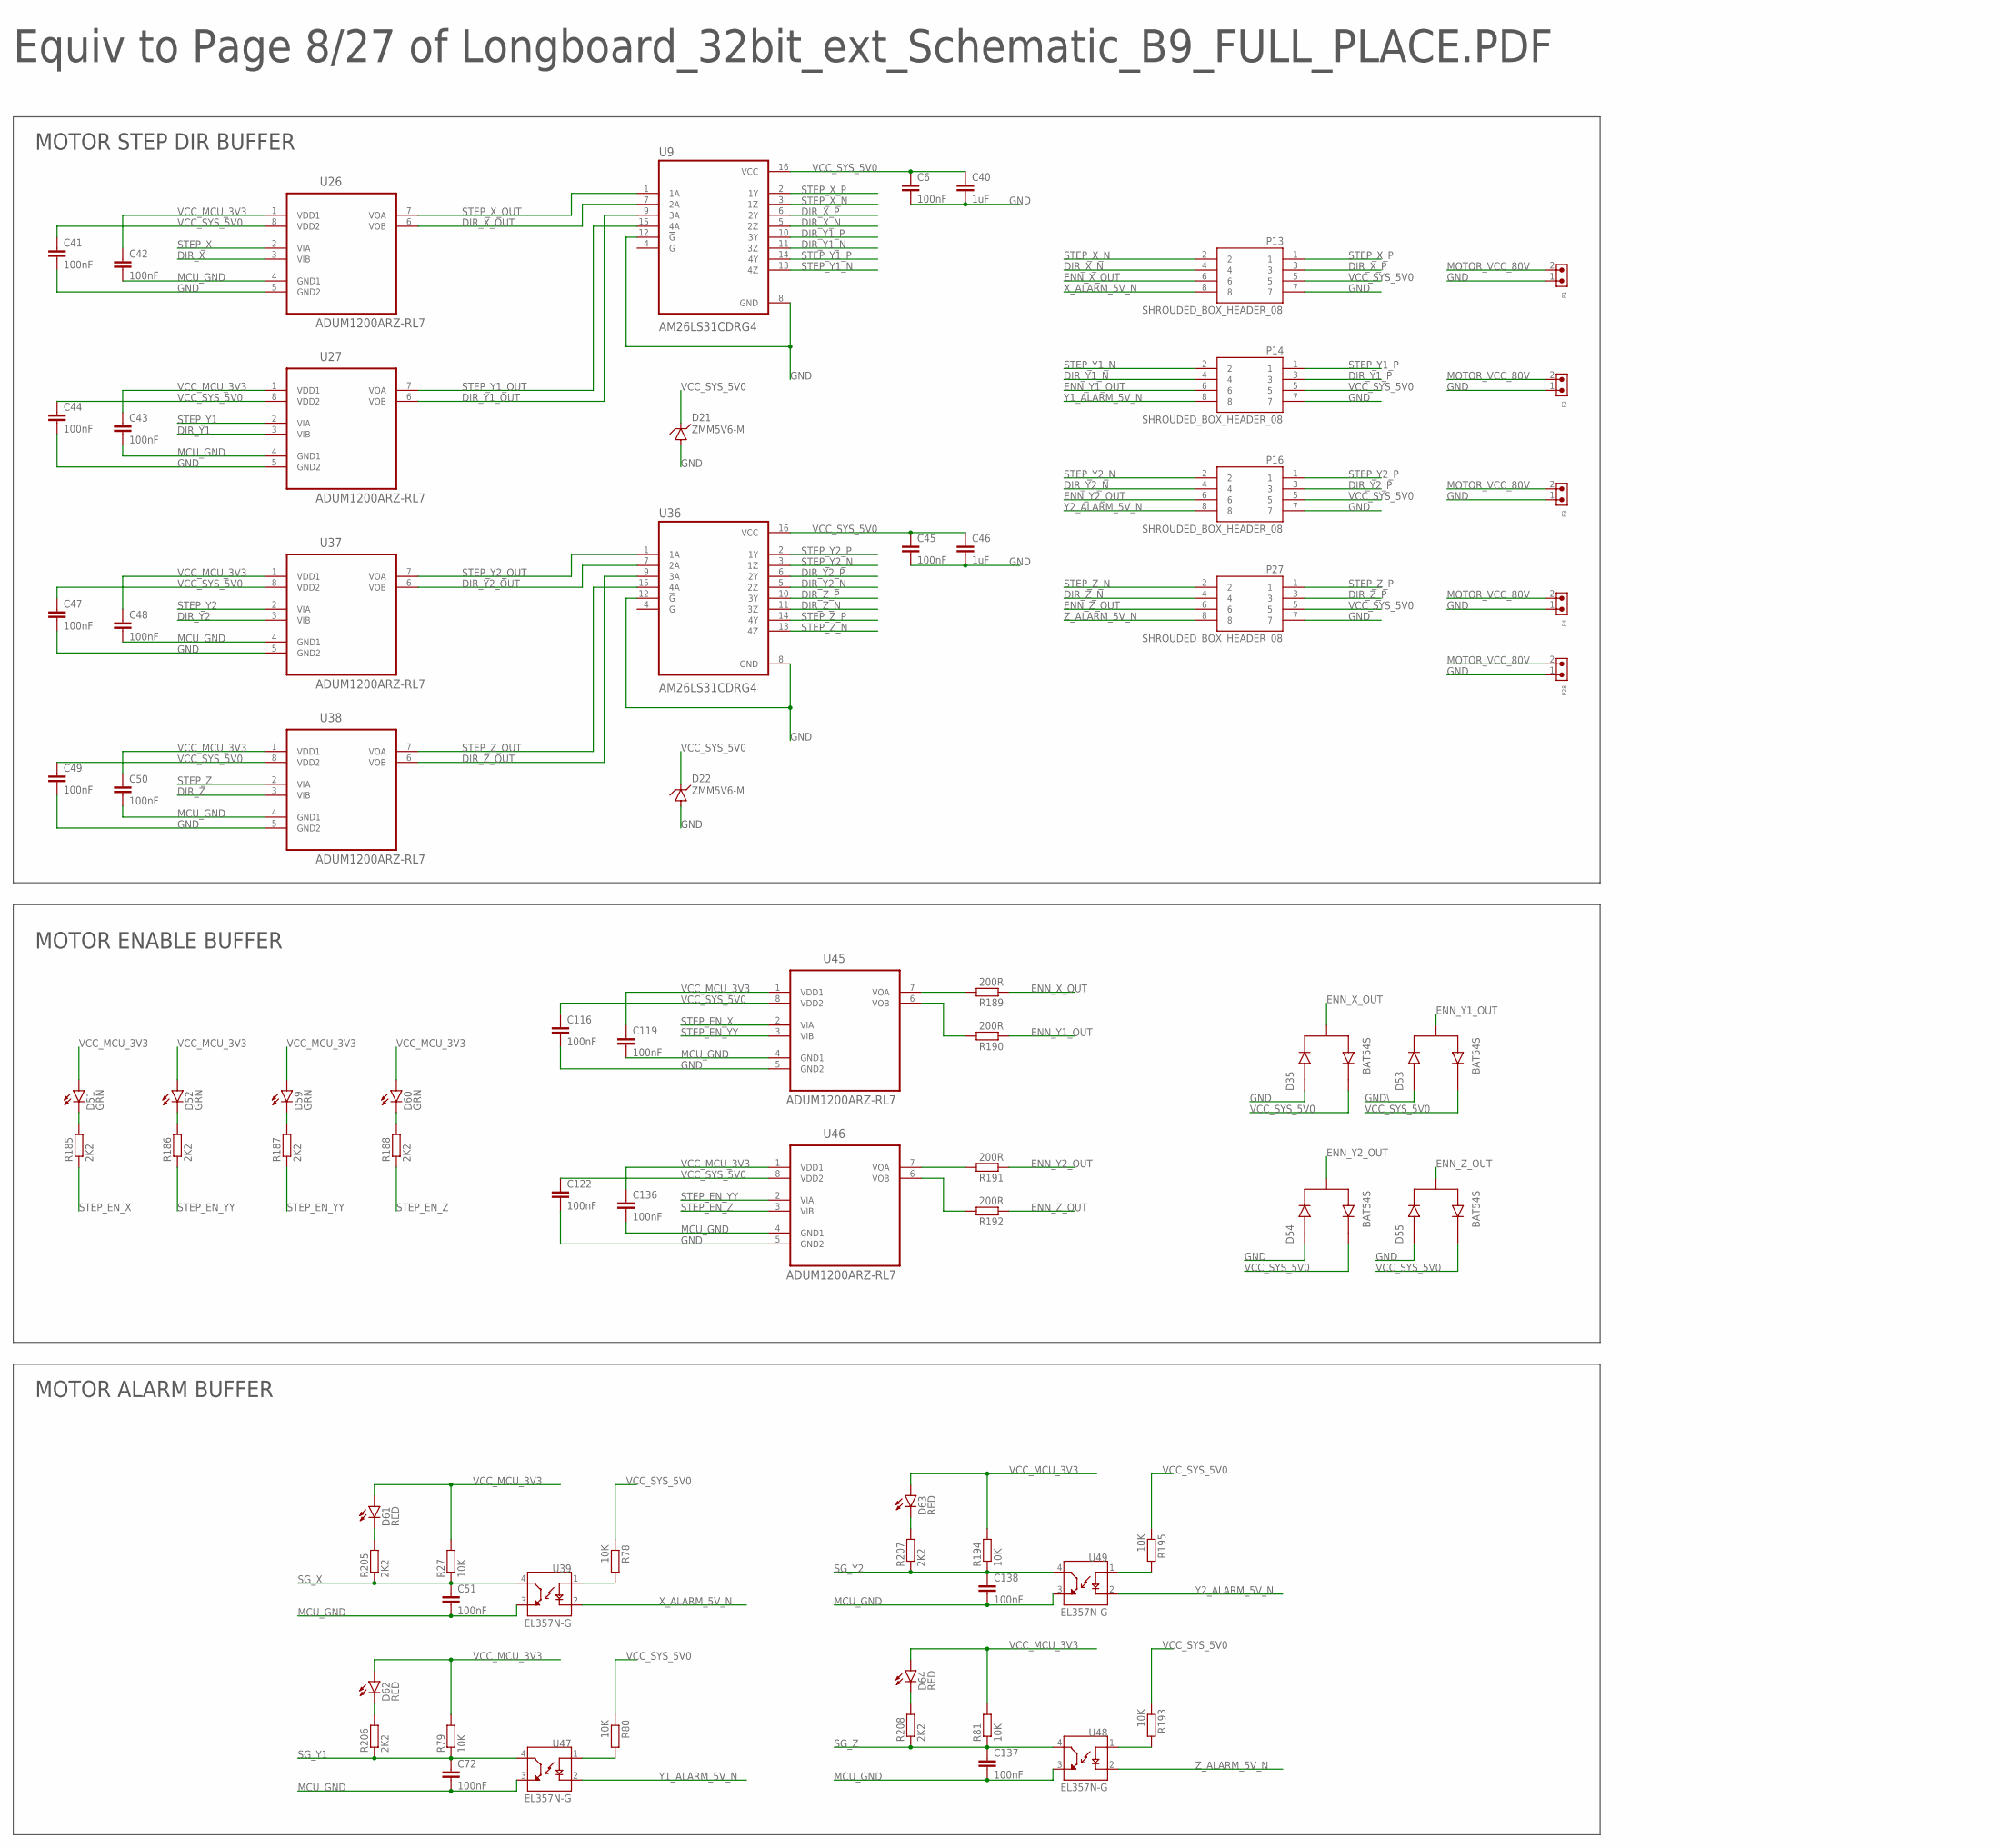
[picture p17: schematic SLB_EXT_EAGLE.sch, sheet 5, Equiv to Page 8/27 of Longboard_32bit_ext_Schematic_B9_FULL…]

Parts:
C6, C41, C42, C43, C44, C45, C47, C48, C49, C50, C51, C116, C119, C122, C136, C137, C138: 100nF; C0603K
C40, C46: 1uF; C0603K
C72: 100nF; C0402
D21, D22: ZMM5V6-M; MINIMELF
D35, D53, D54, D55: BAT54S; SOT95P240X120-3N
D51, D52, D59, D60: GRN; CHIP-LED0603
D61, D62, D63, D64: RED; CHIP-LED0603
P1, P2, P3, P4, P28: DB2EVC-3.81-2P-GN
P13, P14, P16, P27: SHROUDED_BOX_HEADER_08
R27, R79, R81, R194: 10K; R0402
R78, R80, R193, R195: 10K; R0603
R185, R186, R187, R188, R205, R206, R207, R208: 2K2; R0402
R189, R190, R191, R192: 200R; R0603
U9, U36: AM26LS31CDRG4; SOIC127P600X175-16N
U26, U27, U37, U38, U45, U46: ADUM1200ARZ-RL7; SOIC127P600X175-8N
U39, U47, U48, U49: EL357N-G; OPTO_EL357N-G

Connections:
DIR_X: U26.3 (VIB); also elsewhere on the board
DIR_X_N: P13.4, U9.5 (2Z)
DIR_X_OUT: U9.7 (2A), U26.6 (VOB)
DIR_X_P: P13.3, U9.6 (2Y)
DIR_Y1: U27.3 (VIB); also elsewhere on the board
DIR_Y1_N: P14.4, U9.11 (3Z)
DIR_Y1_OUT: U9.9 (3A), U27.6 (VOB)
DIR_Y1_P: P14.3, U9.10 (3Y)
DIR_Y2: U37.3 (VIB); also elsewhere on the board
DIR_Y2_N: P16.4, U36.5 (2Z)
DIR_Y2_OUT: U36.7 (2A), U37.6 (VOB)
DIR_Y2_P: P16.3, U36.6 (2Y)
DIR_Z: U38.3 (VIB); also elsewhere on the board
DIR_Z_N: P27.4, U36.11 (3Z)
DIR_Z_OUT: U36.9 (3A), U38.6 (VOB)
DIR_Z_P: P27.3, U36.10 (3Y)
ENN_X_OUT: D35.3, P13.6, R189.1
ENN_Y1_OUT: D53.3, P14.6, R190.1
ENN_Y2_OUT: D54.3, P16.6, R191.1
ENN_Z_OUT: D55.3, P27.6, R192.1
GND: C6.2, C40.2, C41.2, C44.2, C45.2, C46.2, C47.2, C49.2, C116.2, C122.2, D21.A, D22.A, D35.1, D54.1, D55.1, P1.1, P2.1, P3.1, P4.1, P13.7, P14.7, P16.7, P27.7, P28.1, U9.8 (GND), U9.12 (!G), U26.5 (GND2), U27.5 (GND2), U36.8 (GND), U36.12 (!G), U37.5 (GND2), U38.5 (GND2), U45.5 (GND2), U46.5 (GND2); also elsewhere on the board
GND\: D53.1
MCU_GND: C42.2, C43.2, C48.2, C50.2, C51.2, C72.2, C119.2, C136.2, C137.2, C138.2, U26.4 (GND1), U27.4 (GND1), U37.4 (GND1), U38.4 (GND1), U39.3 (ET), U45.4 (GND1), U46.4 (GND1), U47.3 (ET), U48.3 (ET), U49.3 (ET); also elsewhere on the board
MOTOR_VCC_80V: P1.2, P2.2, P3.2, P4.2, P28.2; also elsewhere on the board
unnamed: R189.2, U45.7 (VOA)
unnamed: R190.2, U45.6 (VOB)
unnamed: R191.2, U46.7 (VOA)
unnamed: R192.2, U46.6 (VOB)
unnamed: R78.2, U39.1 (A)
unnamed: D62.C, R206.2
unnamed: D61.C, R205.2
unnamed: R80.2, U47.1 (A)
unnamed: D63.C, R207.2
unnamed: R195.2, U49.1 (A)
unnamed: D64.C, R208.2
unnamed: R193.2, U48.1 (A)
unnamed: D51.C, R185.2
unnamed: D52.C, R186.2
unnamed: D59.C, R187.2
unnamed: D60.C, R188.2
SG_X: C51.1, R27.1, R205.1, U39.4 (CT); also elsewhere on the board
SG_Y1: C72.1, R79.1, R206.1, U47.4 (CT); also elsewhere on the board
SG_Y2: C138.1, R194.1, R207.1, U49.4 (CT); also elsewhere on the board
SG_Z: C137.1, R81.1, R208.1, U48.4 (CT); also elsewhere on the board
STEP_EN_X: R185.1, U45.2 (VIA); also elsewhere on the board
STEP_EN_YY: R186.1, R187.1, U45.3 (VIB), U46.2 (VIA); also elsewhere on the board
STEP_EN_Z: R188.1, U46.3 (VIB); also elsewhere on the board
STEP_X: U26.2 (VIA); also elsewhere on the board
STEP_X_N: P13.2, U9.3 (1Z)
STEP_X_OUT: U9.1 (1A), U26.7 (VOA)
STEP_X_P: P13.1, U9.2 (1Y)
STEP_Y1: U27.2 (VIA); also elsewhere on the board
STEP_Y1_N: P14.2, U9.13 (4Z)
STEP_Y1_OUT: U9.15 (4A), U27.7 (VOA)
STEP_Y1_P: P14.1, U9.14 (4Y)
STEP_Y2: U37.2 (VIA); also elsewhere on the board
STEP_Y2_N: P16.2, U36.3 (1Z)
STEP_Y2_OUT: U36.1 (1A), U37.7 (VOA)
STEP_Y2_P: P16.1, U36.2 (1Y)
STEP_Z: U38.2 (VIA); also elsewhere on the board
STEP_Z_N: P27.2, U36.13 (4Z)
STEP_Z_OUT: U36.15 (4A), U38.7 (VOA)
STEP_Z_P: P27.1, U36.14 (4Y)
VCC_MCU_3V3: C42.1, C43.1, C48.1, C50.1, C119.1, C136.1, D51.A, D52.A, D59.A, D60.A, D61.A, D62.A, D63.A, D64.A, R27.2, R79.2, R81.2, R194.2, U26.1 (VDD1), U27.1 (VDD1), U37.1 (VDD1), U38.1 (VDD1), U45.1 (VDD1), U46.1 (VDD1); also elsewhere on the board
VCC_SYS_5V0: C6.1, C40.1, C41.1, C44.1, C45.1, C46.1, C47.1, C49.1, C116.1, C122.1, D21.C, D22.C, D35.2, D53.2, D54.2, D55.2, P13.5, P14.5, P16.5, P27.5, R78.1, R80.1, R193.1, R195.1, U9.16 (VCC), U26.8 (VDD2), U27.8 (VDD2), U36.16 (VCC), U37.8 (VDD2), U38.8 (VDD2), U45.8 (VDD2), U46.8 (VDD2); also elsewhere on the board
X_ALARM_5V_N: P13.8, U39.2 (C)
Y1_ALARM_5V_N: P14.8, U47.2 (C)
Y2_ALARM_5V_N: P16.8, U49.2 (C)
Z_ALARM_5V_N: P27.8, U48.2 (C)

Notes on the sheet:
Equiv to Page 8/27 of Longboard_32bit_ext_Schematic_B9_FULL_PLACE.PDF
MOTOR STEP DIR BUFFER
MOTOR ENABLE BUFFER
MOTOR ALARM BUFFER

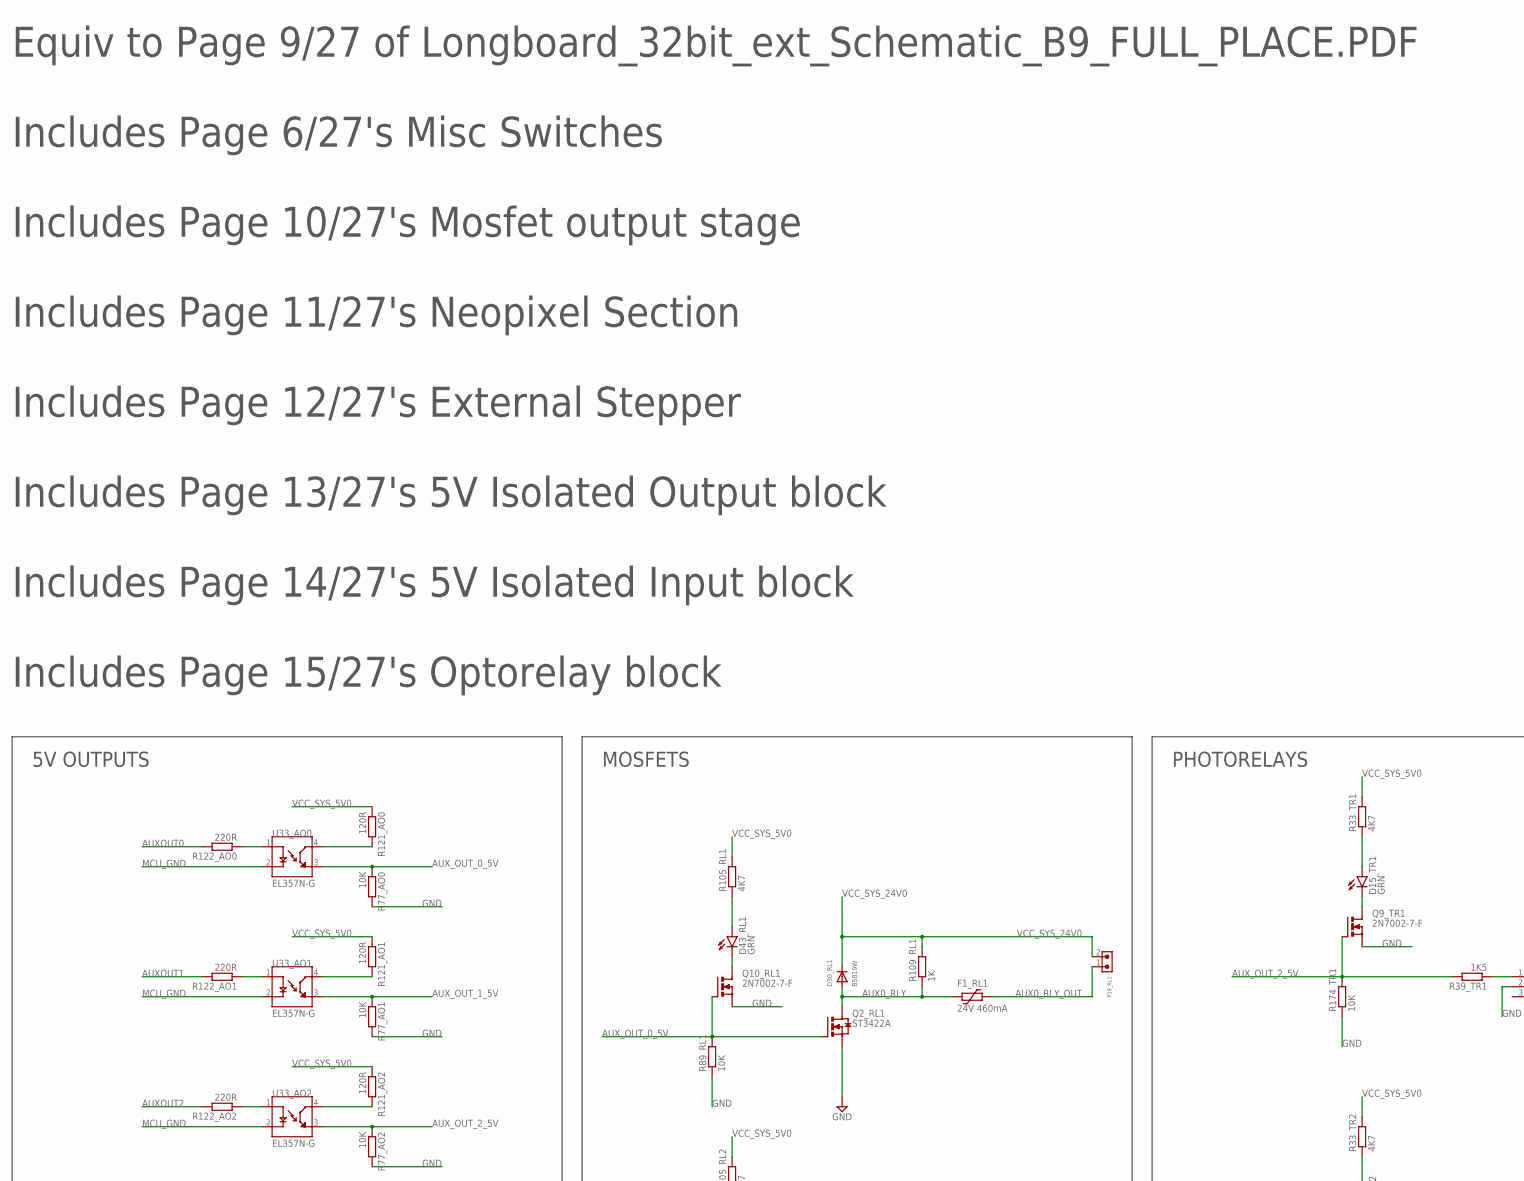
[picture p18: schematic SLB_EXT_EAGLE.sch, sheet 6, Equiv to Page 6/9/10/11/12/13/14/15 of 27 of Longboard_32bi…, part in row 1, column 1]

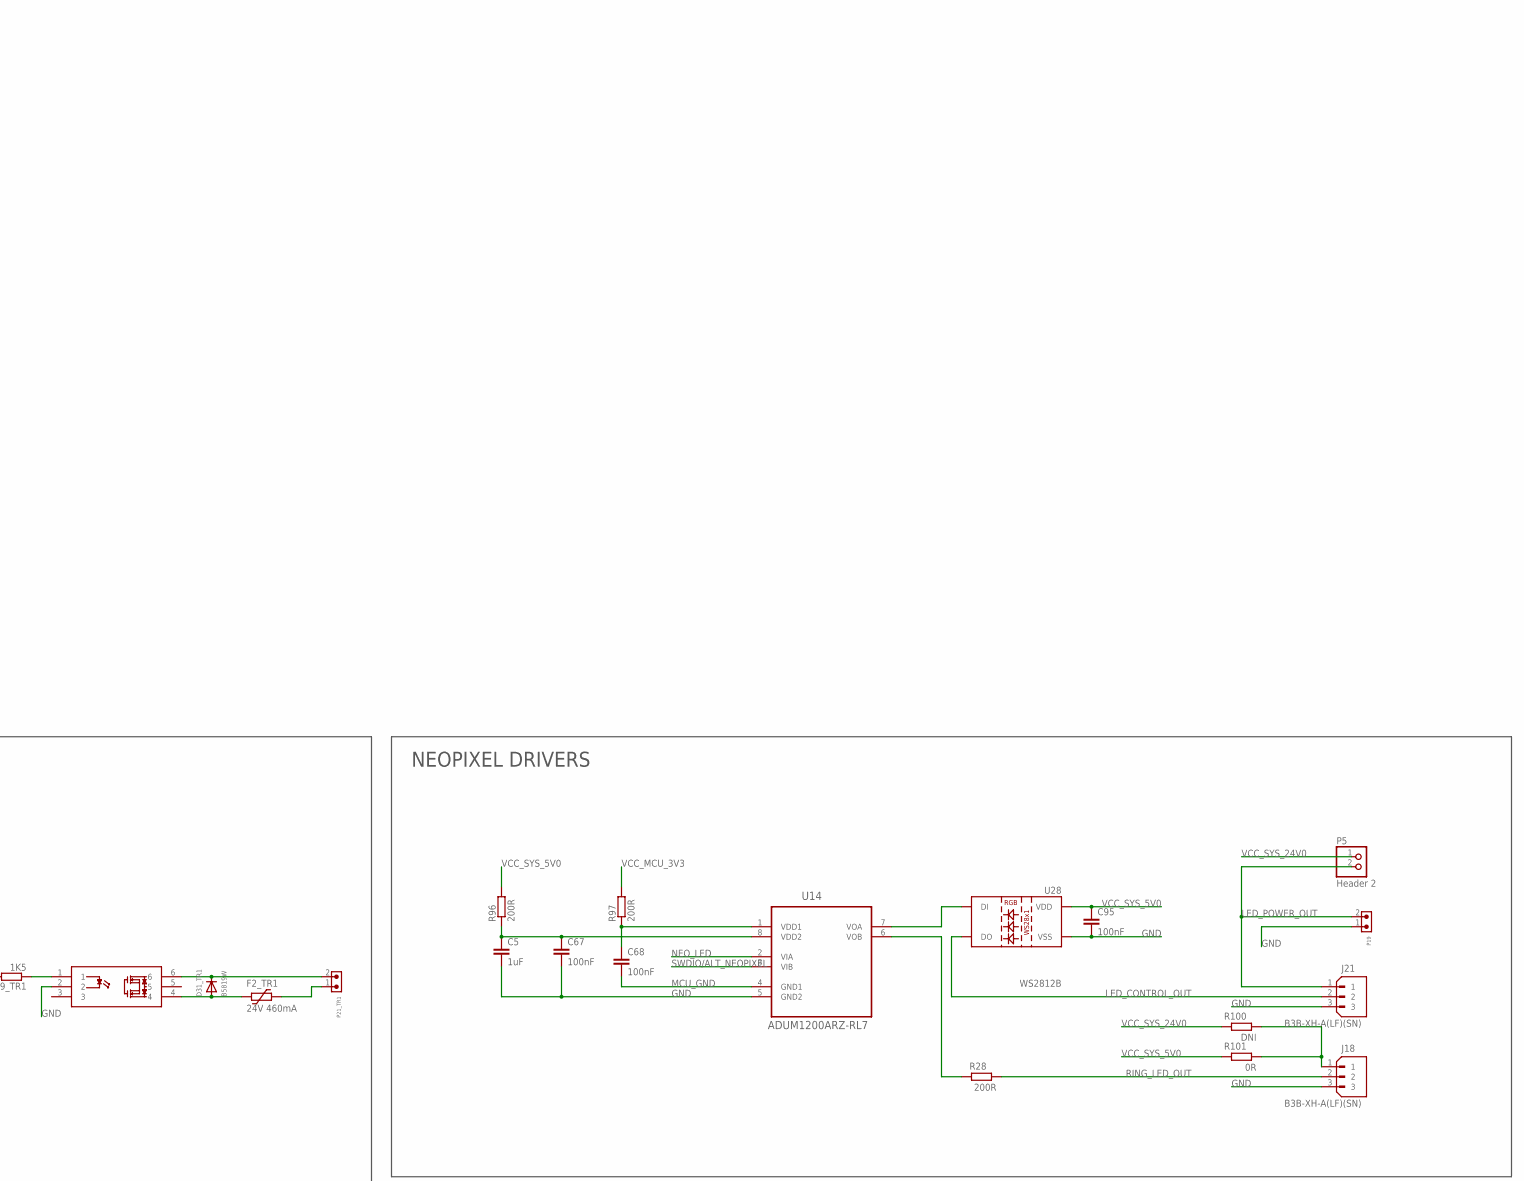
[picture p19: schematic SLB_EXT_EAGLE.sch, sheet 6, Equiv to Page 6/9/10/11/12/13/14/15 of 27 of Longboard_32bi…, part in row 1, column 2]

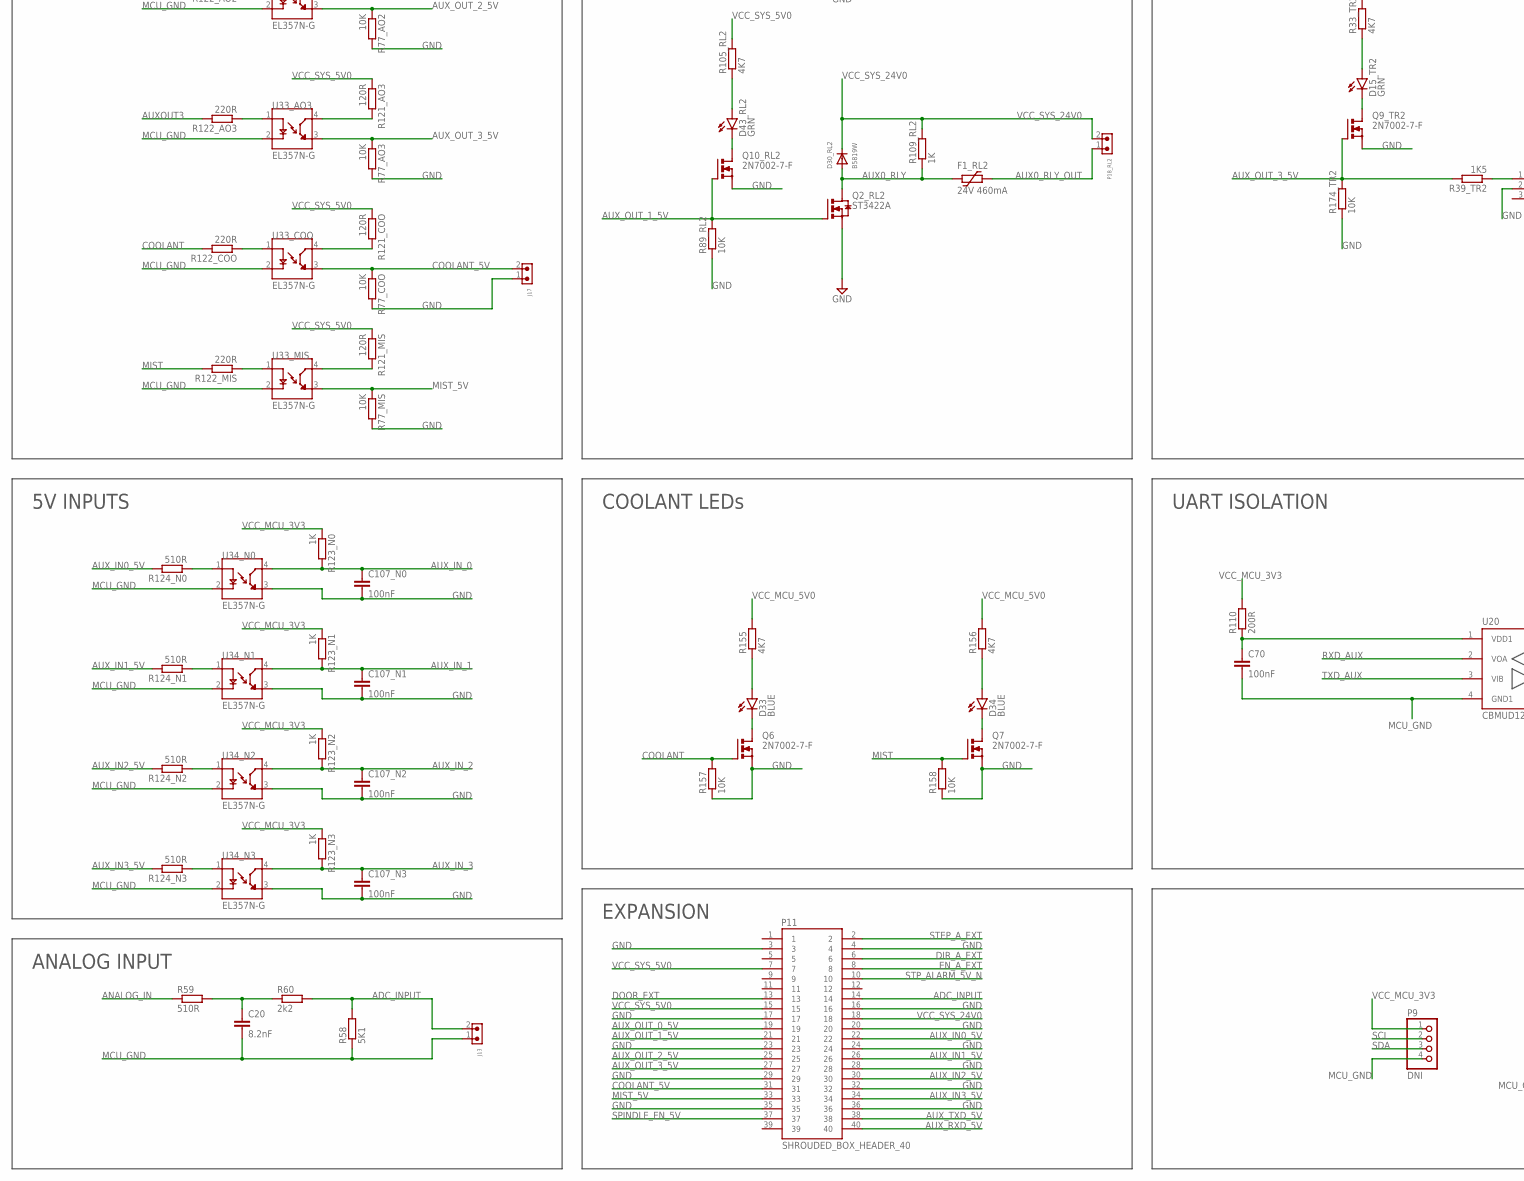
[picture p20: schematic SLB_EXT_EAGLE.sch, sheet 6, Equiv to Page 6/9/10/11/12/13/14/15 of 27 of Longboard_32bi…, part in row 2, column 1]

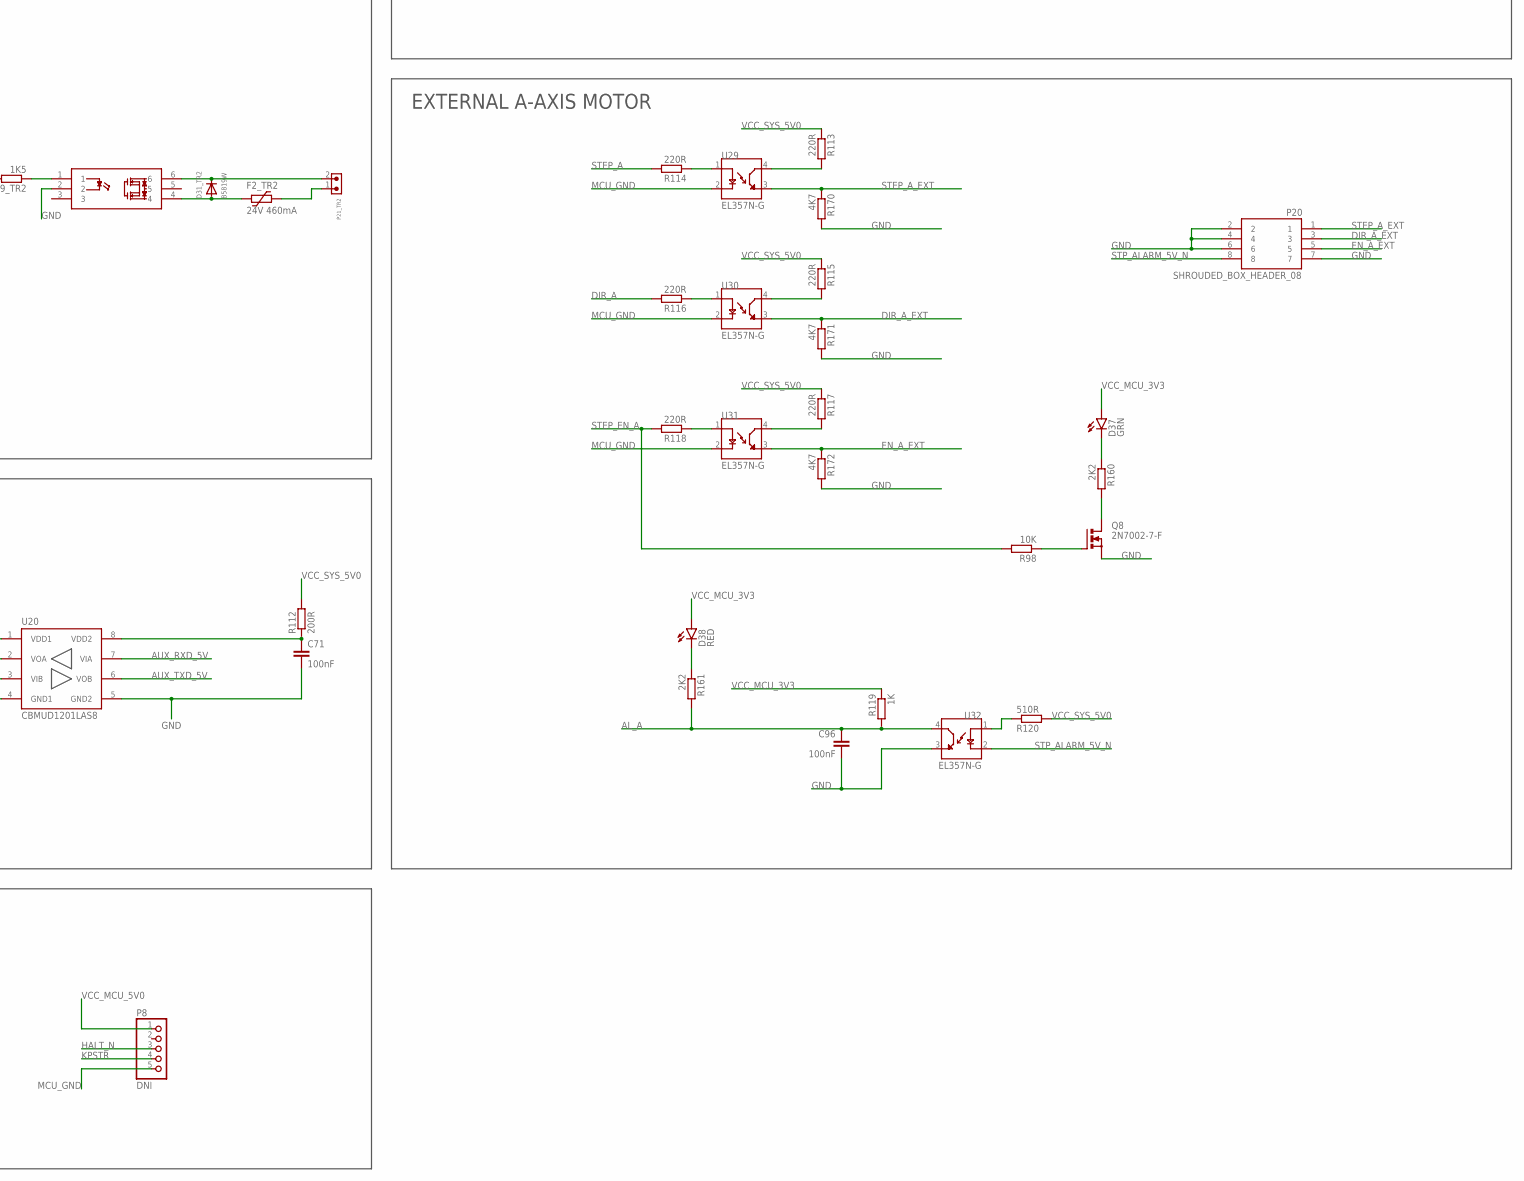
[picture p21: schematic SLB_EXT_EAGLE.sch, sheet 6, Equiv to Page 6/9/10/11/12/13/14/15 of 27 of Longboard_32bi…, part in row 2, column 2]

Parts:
C5: 1uF; C0603K
C20: 8.2nF; C0603K
C67, C68, C95: 100nF; C0603K
C70, C71, C96, C107_N0, C107_N1, C107_N2, C107_N3: 100nF; C0402
D15_TR1, D15_TR2, D37, D43_RL1, D43_RL2: GRN; CHIP-LED0603
D30_RL1, D30_RL2, D31_TR1, D31_TR2: B5819W; SOD123FL
D33, D34: BLUE; CHIP-LED0603
D38: RED; CHIP-LED0603
F1_RL1, F1_RL2, F2_TR1, F2_TR2: 24V 460mA; 1206L
J13, J17: WJ15EDGK-3.81-2P; DB2EVC-3.81-2P-GN
J18, J21: B3B-XH-A(LF)(SN); JST_B3B-XH-A(LF)(SN)
K1_TR1, K1_TR2: TLP3109A
P5: Header 2; 1X02
P8: DNI; 1X05
P9: DNI; 1X04
P11: SHROUDED_BOX_HEADER_40
P18_RL1, P18_RL2, P19, P21_TR1, P21_TR2: WJ15EDGK-3.81-2P; DB2EVC-3.81-2P-GN
P20: SHROUDED_BOX_HEADER_08
Q2_RL1, Q2_RL2: ST3422A; SOT-23
Q6, Q7, Q8, Q9_TR1, Q9_TR2, Q10_RL1, Q10_RL2: 2N7002-7-F; SOT-23
R28, R96, R110, R112: 200R; R0402
R33_TR1, R33_TR2, R105_RL1, R105_RL2, R155, R156, R170, R171, R172: 4K7; R0402
R39_TR1, R39_TR2: 1K5; R0402
R58: 5K1; R0402
R59, R120, R124_N0, R124_N1, R124_N2, R124_N3: 510R; R0402
R60: 2k2; R0402
R77_AO0, R77_AO1, R77_AO2, R77_AO3, R77_COO, R77_MIS, R89_RL1, R89_RL2, R174_TR1, R174_TR2: 10K; R0402
R97: 200R; R0603
R98, R157, R158: 10K; R0603
R100: DNI; R0402
R101: 0R; R0402
R109_RL1, R109_RL2: 1K; R0603
R113, R114, R115, R117, R118, R122_AO0, R122_AO1, R122_AO2, R122_AO3, R122_COO, R122_MIS: 220R; R0402
R116: 220R; R0603
R119, R123_N0, R123_N1, R123_N2, R123_N3: 1K; R0402
R121_AO0, R121_AO1, R121_AO2, R121_AO3, R121_COO, R121_MIS: 120R; R0402
R160, R161: 2K2; R0402
U14: ADUM1200ARZ-RL7; SOIC127P600X175-8N
U20: CBMUD1201LAS8; SOIC-8
U28: WS2812B
U29, U30, U31, U32, U33_AO0, U33_AO1, U33_AO2, U33_AO3, U33_COO, U33_MIS, U34_N0, U34_N1, U34_N2, U34_N3: EL357N-G; OPTO_EL357N-G

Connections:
ADC_INPUT: J13.2, P11.14, R58.2, R60.2
AL_A: C96.1, R119.2, R161.2, U32.4 (CT); also elsewhere on the board
ANALOG_IN: R59.1; also elsewhere on the board
AUX0_RLY: D30_RL1.A, D30_RL2.A, F1_RL1.2, F1_RL2.2, Q2_RL1.P3 (D), Q2_RL2.P3 (D), R109_RL1.1, R109_RL2.1
AUX0_RLY_OUT: F1_RL1.1, F1_RL2.1, P18_RL1.1, P18_RL2.1
AUXOUT0: R122_AO0.2; also elsewhere on the board
AUXOUT1: R122_AO1.2; also elsewhere on the board
AUXOUT2: R122_AO2.2; also elsewhere on the board
AUXOUT3: R122_AO3.2; also elsewhere on the board
AUX_IN0_5V: P11.22, R124_N0.2
AUX_IN1_5V: P11.26, R124_N1.2
AUX_IN2_5V: P11.30, R124_N2.2
AUX_IN3_5V: P11.34, R124_N3.2
AUX_IN_0: C107_N0.1, R123_N0.2, U34_N0.4 (CT); also elsewhere on the board
AUX_IN_1: C107_N1.1, R123_N1.2, U34_N1.4 (CT); also elsewhere on the board
AUX_IN_2: C107_N2.1, R123_N2.2, U34_N2.4 (CT); also elsewhere on the board
AUX_IN_3: C107_N3.1, R123_N3.2, U34_N3.4 (CT); also elsewhere on the board
AUX_OUT_0_5V: P11.19, Q2_RL1.P1 (G), Q10_RL1.P1 (G), R77_AO0.1, R89_RL1.2, U33_AO0.3 (ET)
AUX_OUT_1_5V: P11.21, Q2_RL2.P1 (G), Q10_RL2.P1 (G), R77_AO1.1, R89_RL2.2, U33_AO1.3 (ET)
AUX_OUT_2_5V: P11.25, Q9_TR1.P1 (G), R39_TR1.2, R77_AO2.1, R174_TR1.2, U33_AO2.3 (ET)
AUX_OUT_3_5V: P11.27, Q9_TR2.P1 (G), R39_TR2.2, R77_AO3.1, R174_TR2.2, U33_AO3.3 (ET)
AUX_RXD_5V: P11.40, U20.7 (VIA)
AUX_TXD_5V: P11.38, U20.6 (VOB)
COOLANT: Q6.P1 (G), R122_COO.2, R157.2; also elsewhere on the board
COOLANT_5V: J17.2, P11.31, R77_COO.1, U33_COO.3 (ET)
DIR_A: R116.2; also elsewhere on the board
DIR_A_EXT: P11.6, P20.3, R171.1, U30.3 (ET)
DOOR_EXT: P11.13; also elsewhere on the board
EN_A_EXT: P11.8, P20.5, R172.1, U31.3 (ET)
GND: C5.2, C67.2, C71.2, C95.2, C96.2, C107_N0.2, C107_N1.2, C107_N2.2, C107_N3.2, J17.1, J18.3, J21.3, K1_TR1.2, K1_TR2.2, P11.3, P11.4, P11.16, P11.17, P11.20, P11.23, P11.24, P11.28, P11.29, P11.32, P11.35, P11.36, P19.1, P20.2, P20.4, P20.6, P20.7, Q2_RL1.P2 (S), Q2_RL2.P2 (S), Q6.P2 (S), Q7.P2 (S), Q8.P2 (S), Q9_TR1.P2 (S), Q9_TR2.P2 (S), Q10_RL1.P2 (S), Q10_RL2.P2 (S), R77_AO0.2, R77_AO1.2, R77_AO2.2, R77_AO3.2, R77_COO.2, R77_MIS.2, R89_RL1.1, R89_RL2.1, R157.1, R158.1, R170.2, R171.2, R172.2, R174_TR1.1, R174_TR2.1, U14.5 (GND2), U20.5 (GND2), U28.3 (VSS), U32.3 (ET), U34_N0.3 (ET), U34_N1.3 (ET), U34_N2.3 (ET), U34_N3.3 (ET); also elsewhere on the board
HALT_N: P8.3; also elsewhere on the board
KPSTR: P8.4; also elsewhere on the board
LED_CONTROL_OUT: J21.2, U28.2 (DO)
LED_POWER_OUT: J21.1, P5.2, P19.2
MCU_GND: C20.2, C68.2, C70.2, J13.1, P8.5, P9.4, R58.1, U14.4 (GND1), U20.4 (GND1), U29.2 (C), U30.2 (C), U31.2 (C), U33_AO0.2 (C), U33_AO1.2 (C), U33_AO2.2 (C), U33_AO3.2 (C), U33_COO.2 (C), U33_MIS.2 (C), U34_N0.2 (C), U34_N1.2 (C), U34_N2.2 (C), U34_N3.2 (C); also elsewhere on the board
MIST: Q7.P1 (G), R122_MIS.2, R158.2; also elsewhere on the board
MIST_5V: P11.33, R77_MIS.1, U33_MIS.3 (ET)
unnamed: R122_AO0.1, U33_AO0.1 (A)
unnamed: D43_RL1.A, R105_RL1.1
unnamed: R122_MIS.1, U33_MIS.1 (A)
unnamed: R121_AO0.2, U33_AO0.4 (CT)
unnamed: R122_AO1.1, U33_AO1.1 (A)
unnamed: D43_RL1.C, Q10_RL1.P3 (D)
unnamed: D15_TR1.A, R33_TR1.1
unnamed: R121_AO1.2, U33_AO1.4 (CT)
unnamed: R122_AO2.1, U33_AO2.1 (A)
unnamed: D43_RL2.A, R105_RL2.1
unnamed: D43_RL2.C, Q10_RL2.P3 (D)
unnamed: R121_AO2.2, U33_AO2.4 (CT)
unnamed: R122_AO3.1, U33_AO3.1 (A)
unnamed: R121_MIS.2, U33_MIS.4 (CT)
unnamed: D15_TR1.C, Q9_TR1.P3 (D)
unnamed: R121_AO3.2, U33_AO3.4 (CT)
unnamed: R122_COO.1, U33_COO.1 (A)
unnamed: K1_TR1.1, R39_TR1.1
unnamed: D31_TR1.C, K1_TR1.6, P21_TR1.2
unnamed: R121_COO.2, U33_COO.4 (CT)
unnamed: D31_TR1.A, F2_TR1.2, K1_TR1.4
unnamed: F2_TR1.1, P21_TR1.1
unnamed: D15_TR2.A, R33_TR2.1
unnamed: D15_TR2.C, Q9_TR2.P3 (D)
unnamed: K1_TR2.1, R39_TR2.1
unnamed: D31_TR2.C, K1_TR2.6, P21_TR2.2
unnamed: D31_TR2.A, F2_TR2.2, K1_TR2.4
unnamed: F2_TR2.1, P21_TR2.1
unnamed: R124_N0.1, U34_N0.1 (A)
unnamed: R124_N1.1, U34_N1.1 (A)
unnamed: R124_N2.1, U34_N2.1 (A)
unnamed: R120.1, U32.1 (A)
unnamed: D33.A, R155.1
unnamed: D33.C, Q6.P3 (D)
unnamed: D34.A, R156.1
unnamed: D34.C, Q7.P3 (D)
unnamed: C5.1, C67.1, R96.1, U14.8 (VDD2)
unnamed: C68.1, R97.1, U14.1 (VDD1)
unnamed: C70.1, R110.1, U20.1 (VDD1)
unnamed: C71.1, R112.1, U20.8 (VDD2)
unnamed: R28.2, U14.6 (VOB)
unnamed: U14.7 (VOA), U28.4 (DI)
unnamed: R114.1, U29.1 (A)
unnamed: R113.2, U29.4 (CT)
unnamed: R116.1, U30.1 (A)
unnamed: R115.2, U30.4 (CT)
unnamed: R118.1, U31.1 (A)
unnamed: R117.2, U31.4 (CT)
unnamed: D37.C, R160.1
unnamed: Q8.P3 (D), R160.2
unnamed: Q8.P1 (G), R98.1
unnamed: D38.C, R161.1
unnamed: C20.1, R59.2, R60.1
unnamed: J18.1, R100.1, R101.1
unnamed: R124_N3.1, U34_N3.1 (A)
NEO_LED: U14.2 (VIA); also elsewhere on the board
RING_LED_OUT: J18.2, R28.1
RXD_AUX: U20.2 (VOA); also elsewhere on the board
SCL: P9.2; also elsewhere on the board
SDA: P9.3; also elsewhere on the board
SPINDLE_EN_5V: P11.37; also elsewhere on the board
STEP_A: R114.2; also elsewhere on the board
STEP_A_EXT: P11.2, P20.1, R170.1, U29.3 (ET)
STEP_EN_A: R98.2, R118.2; also elsewhere on the board
STP_ALARM_5V_N: P11.10, P20.8, U32.2 (C)
SWDIO/ALT_NEOPIXEL: U14.3 (VIB); also elsewhere on the board
TXD_AUX: U20.3 (VIB); also elsewhere on the board
VCC_MCU_3V3: D37.A, D38.A, P9.1, R97.2, R110.2, R119.1, R123_N0.1, R123_N1.1, R123_N2.1, R123_N3.1; also elsewhere on the board
VCC_MCU_5V0: P8.1, R155.2, R156.2; also elsewhere on the board
VCC_SYS_5V0: C95.1, P11.7, P11.15, R33_TR1.2, R33_TR2.2, R96.2, R101.2, R105_RL1.2, R105_RL2.2, R112.2, R113.1, R115.1, R117.1, R120.2, R121_AO0.1, R121_AO1.1, R121_AO2.1, R121_AO3.1, R121_COO.1, R121_MIS.1, U28.1 (VDD); also elsewhere on the board
VCC_SYS_24V0: D30_RL1.C, D30_RL2.C, P5.1, P11.18, P18_RL1.2, P18_RL2.2, R100.2, R109_RL1.2, R109_RL2.2; also elsewhere on the board

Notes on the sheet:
Equiv to Page 9/27 of Longboard_32bit_ext_Schematic_B9_FULL_PLACE.PDF Includes Page 6/27's Misc Switches Includes Page 10/27's Mosfet output stage Includes Page 11/27's Neopixel Section Includes Page 12/27's External Stepper Includes Page 13/27's 5V Isolated Output block Includes Page 14/27's 5V Is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
5V OUTPUTS
MOSFETS
PHOTORELAYS
5V INPUTS
COOLANT LEDs
UART ISOLATION
NEOPIXEL DRIVERS
EXTERNAL A-AXIS MOTOR
ANALOG INPUT
EXPANSION

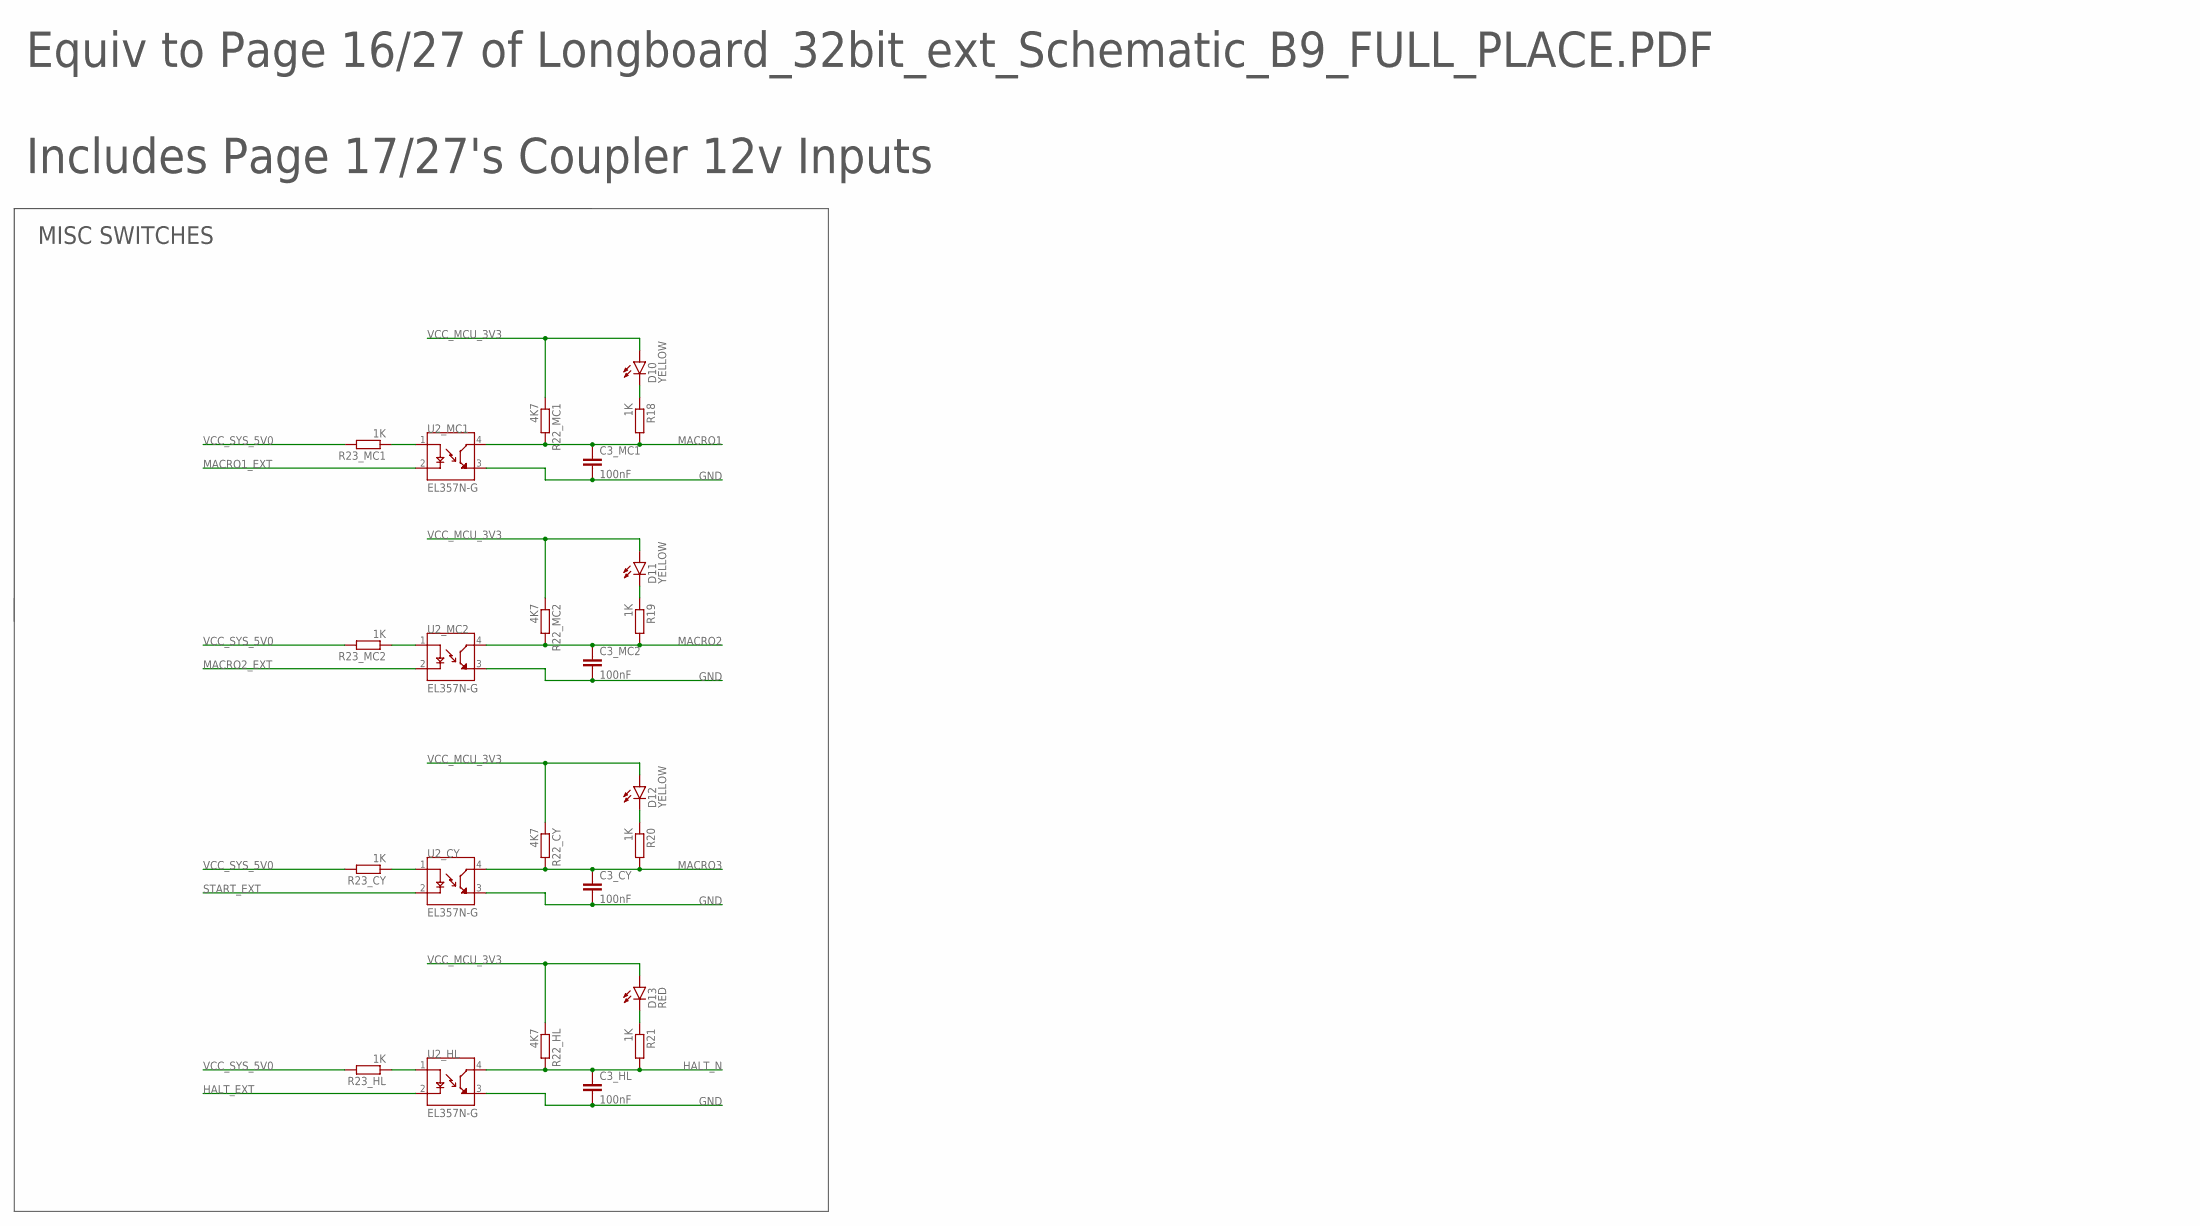
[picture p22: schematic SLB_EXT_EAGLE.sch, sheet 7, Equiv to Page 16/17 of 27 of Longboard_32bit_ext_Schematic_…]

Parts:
C3_CY: 100nF; C0603K
C3_HL, C3_MC1, C3_MC2: 100nF; C0402
D10, D11, D12: YELLOW; CHIP-LED0603
D13: RED; CHIP-LED0603
R18, R19, R20, R21: 1K; R0402
R22_CY: 4K7; R0603
R22_HL, R22_MC1, R22_MC2: 4K7; R0402
R23_CY, R23_HL, R23_MC1, R23_MC2: 1K; R0603
U2_CY, U2_HL, U2_MC1, U2_MC2: EL357N-G; OPTO_EL357N-G

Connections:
GND: C3_CY.2, C3_HL.2, C3_MC1.2, C3_MC2.2, U2_CY.3 (ET), U2_HL.3 (ET), U2_MC1.3 (ET), U2_MC2.3 (ET); also elsewhere on the board
HALT_EXT: U2_HL.2 (C); also elsewhere on the board
HALT_N: C3_HL.1, R21.2, R22_HL.2, U2_HL.4 (CT); also elsewhere on the board
MACRO1: C3_MC1.1, R18.2, R22_MC1.2, U2_MC1.4 (CT); also elsewhere on the board
MACRO1_EXT: U2_MC1.2 (C); also elsewhere on the board
MACRO2: C3_MC2.1, R19.2, R22_MC2.2, U2_MC2.4 (CT); also elsewhere on the board
MACRO2_EXT: U2_MC2.2 (C); also elsewhere on the board
MACRO3: C3_CY.1, R20.2, R22_CY.2, U2_CY.4 (CT); also elsewhere on the board
unnamed: R23_MC1.1, U2_MC1.1 (A)
unnamed: D10.C, R18.1
unnamed: R23_MC2.1, U2_MC2.1 (A)
unnamed: D11.C, R19.1
unnamed: R23_CY.1, U2_CY.1 (A)
unnamed: D12.C, R20.1
unnamed: R23_HL.1, U2_HL.1 (A)
unnamed: D13.C, R21.1
START_EXT: U2_CY.2 (C); also elsewhere on the board
VCC_MCU_3V3: D10.A, D11.A, D12.A, D13.A, R22_CY.1, R22_HL.1, R22_MC1.1, R22_MC2.1; also elsewhere on the board
VCC_SYS_5V0: R23_CY.2, R23_HL.2, R23_MC1.2, R23_MC2.2; also elsewhere on the board

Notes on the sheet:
Equiv to Page 16/27 of Longboard_32bit_ext_Schematic_B9_FULL_PLACE.PDF Includes Page 17/27's Coupler 12v Inputs
MISC SWITCHES

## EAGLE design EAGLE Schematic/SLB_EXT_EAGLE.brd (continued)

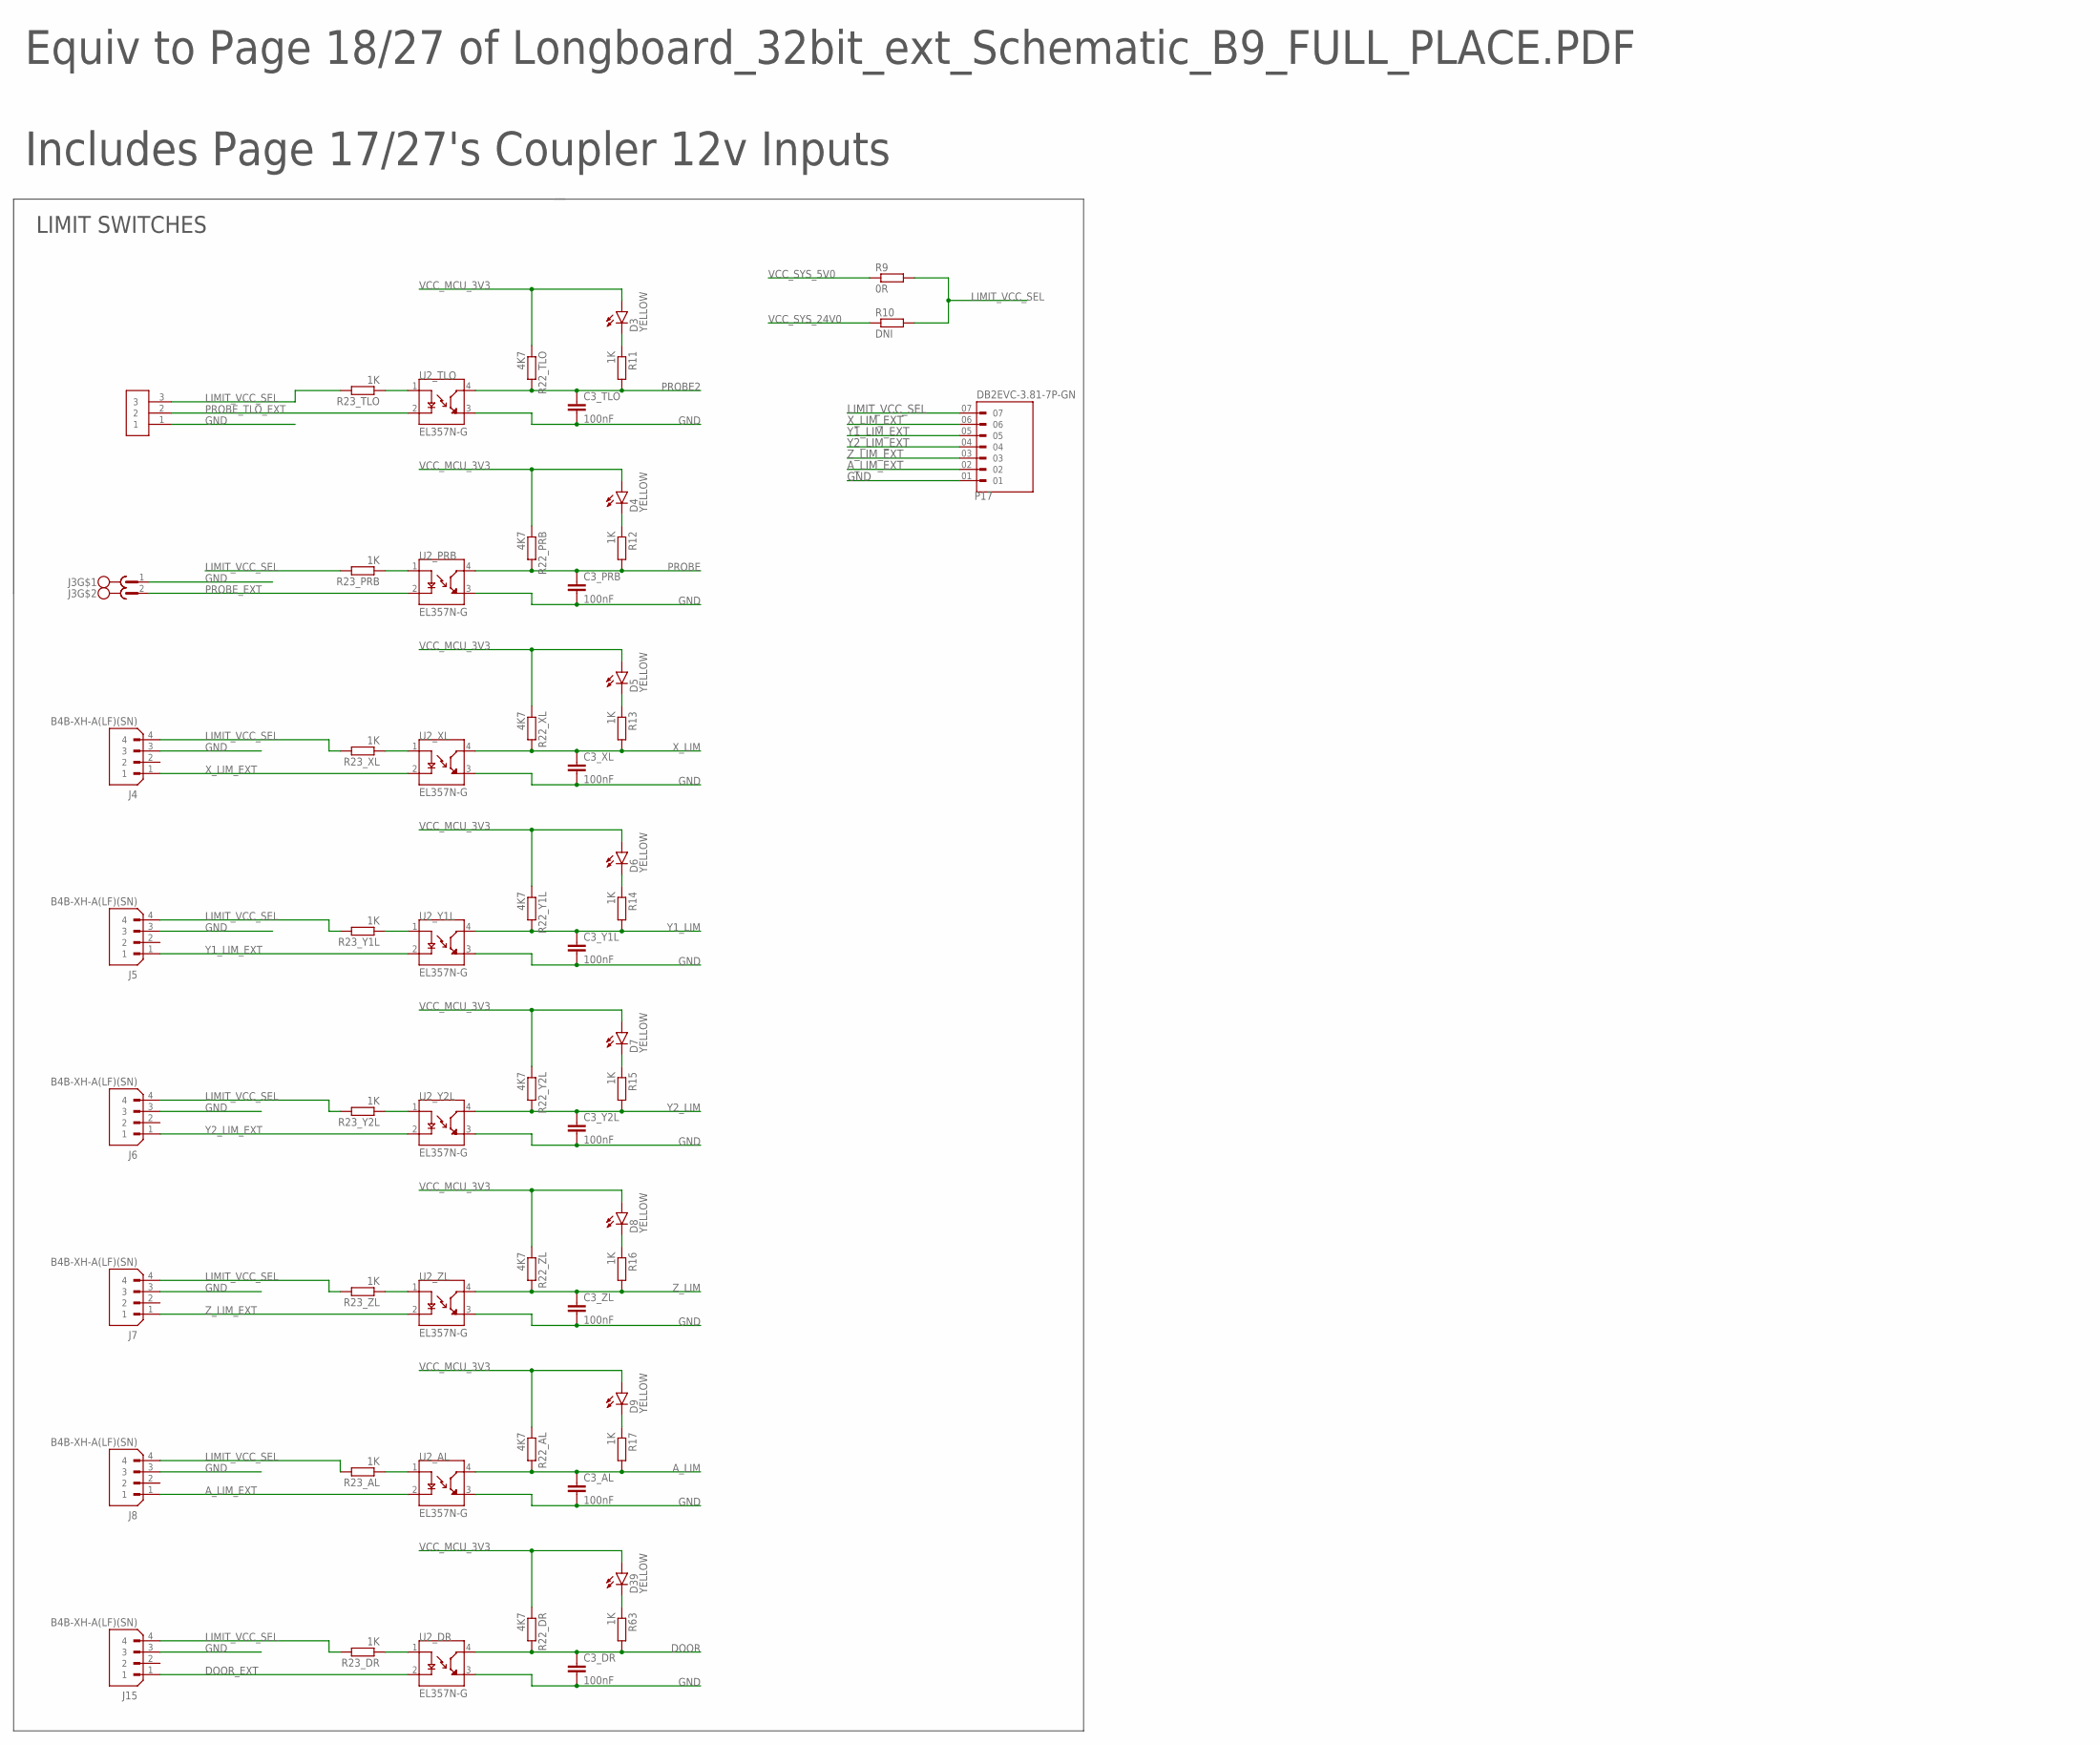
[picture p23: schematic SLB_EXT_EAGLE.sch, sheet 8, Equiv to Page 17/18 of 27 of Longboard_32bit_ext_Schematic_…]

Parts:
C3_AL, C3_DR, C3_PRB, C3_TLO, C3_XL, C3_Y1L, C3_Y2L, C3_ZL: 100nF; C0402
D3, D4, D5, D6, D7, D8, D9, D39: YELLOW; CHIP-LED0603
J2: Phoenix Pluggable 3.81mm 3 way; 3.81MM-3WAY-PLUGGABLE-SCREW
J3: Phoenix Pluggable 3.81mm 2 way; MC1.5/2-G-3.81
J4, J5, J6, J7, J8, J15: B4B-XH-A(LF)(SN); JST_B4B-XH-A(LF)(SN)
P17: DB2EVC-3.81-7P-GN; PHOENIX_1803471
R9: 0R; R0603
R10: DNI; R0603
R11, R12, R13, R14, R15, R16, R17, R63: 1K; R0402
R22_AL, R22_DR, R22_PRB, R22_TLO, R22_XL, R22_Y1L, R22_Y2L, R22_ZL: 4K7; R0402
R23_AL, R23_DR, R23_PRB, R23_TLO, R23_XL, R23_Y1L, R23_Y2L, R23_ZL: 1K; R0603
U2_AL, U2_DR, U2_PRB, U2_TLO, U2_XL, U2_Y1L, U2_Y2L, U2_ZL: EL357N-G; OPTO_EL357N-G

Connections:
A_LIM: C3_AL.1, R17.2, R22_AL.2, U2_AL.4 (CT); also elsewhere on the board
A_LIM_EXT: J8.1, P17.02, U2_AL.2 (C)
DOOR: C3_DR.1, R22_DR.2, R63.2, U2_DR.4 (CT); also elsewhere on the board
DOOR_EXT: J15.1, U2_DR.2 (C); also elsewhere on the board
GND: C3_AL.2, C3_DR.2, C3_PRB.2, C3_TLO.2, C3_XL.2, C3_Y1L.2, C3_Y2L.2, C3_ZL.2, J2.1, J3.1, J4.3, J5.3, J6.3, J7.3, J8.3, J15.3, P17.01, U2_AL.3 (ET), U2_DR.3 (ET), U2_PRB.3 (ET), U2_TLO.3 (ET), U2_XL.3 (ET), U2_Y1L.3 (ET), U2_Y2L.3 (ET), U2_ZL.3 (ET); also elsewhere on the board
LIMIT_VCC_SEL: J2.3, J4.4, J5.4, J6.4, J7.4, J8.4, J15.4, P17.07, R9.2, R10.2, R23_AL.2, R23_DR.2, R23_PRB.2, R23_TLO.2, R23_XL.2, R23_Y1L.2, R23_Y2L.2, R23_ZL.2
unnamed: R23_TLO.1, U2_TLO.1 (A)
unnamed: D3.C, R11.1
unnamed: R23_PRB.1, U2_PRB.1 (A)
unnamed: D4.C, R12.1
unnamed: R23_XL.1, U2_XL.1 (A)
unnamed: D5.C, R13.1
unnamed: R23_Y1L.1, U2_Y1L.1 (A)
unnamed: D6.C, R14.1
unnamed: R23_Y2L.1, U2_Y2L.1 (A)
unnamed: D7.C, R15.1
unnamed: R23_ZL.1, U2_ZL.1 (A)
unnamed: D8.C, R16.1
unnamed: R23_AL.1, U2_AL.1 (A)
unnamed: D9.C, R17.1
unnamed: R23_DR.1, U2_DR.1 (A)
unnamed: D39.C, R63.1
PROBE: C3_PRB.1, R12.2, R22_PRB.2, U2_PRB.4 (CT); also elsewhere on the board
PROBE2: C3_TLO.1, R11.2, R22_TLO.2, U2_TLO.4 (CT); also elsewhere on the board
PROBE_EXT: J3.2, U2_PRB.2 (C)
PROBE_TLO_EXT: J2.2, U2_TLO.2 (C)
VCC_MCU_3V3: D3.A, D4.A, D5.A, D6.A, D7.A, D8.A, D9.A, D39.A, R22_AL.1, R22_DR.1, R22_PRB.1, R22_TLO.1, R22_XL.1, R22_Y1L.1, R22_Y2L.1, R22_ZL.1; also elsewhere on the board
VCC_SYS_5V0: R9.1; also elsewhere on the board
VCC_SYS_24V0: R10.1; also elsewhere on the board
X_LIM: C3_XL.1, R13.2, R22_XL.2, U2_XL.4 (CT); also elsewhere on the board
X_LIM_EXT: J4.1, P17.06, U2_XL.2 (C)
Y1_LIM: C3_Y1L.1, R14.2, R22_Y1L.2, U2_Y1L.4 (CT); also elsewhere on the board
Y1_LIM_EXT: J5.1, P17.05, U2_Y1L.2 (C)
Y2_LIM: C3_Y2L.1, R15.2, R22_Y2L.2, U2_Y2L.4 (CT); also elsewhere on the board
Y2_LIM_EXT: J6.1, P17.04, U2_Y2L.2 (C)
Z_LIM: C3_ZL.1, R16.2, R22_ZL.2, U2_ZL.4 (CT); also elsewhere on the board
Z_LIM_EXT: J7.1, P17.03, U2_ZL.2 (C)

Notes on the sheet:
Equiv to Page 18/27 of Longboard_32bit_ext_Schematic_B9_FULL_PLACE.PDF Includes Page 17/27's Coupler 12v Inputs
LIMIT SWITCHES

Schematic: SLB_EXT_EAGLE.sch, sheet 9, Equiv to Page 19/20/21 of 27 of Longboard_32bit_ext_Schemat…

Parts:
C10: 100nF; C0402; LCSC_PART C576517
C11, C12, C14, C15, C58, C59: 10uF; C1206; LCSC_PART C576517
C13, C52, C53: 22uF; C0805; LCSC_PART C576517
C16: 10nF; C0402; LCSC_PART C576517
C17: 10pF; C0603; LCSC_PART C576517
C18, C19, C85: 8.2nF; C0603; LCSC_PART C576517
C54: 4.7uF; C0603
C55: 22uF; C0603; LCSC_PART C576517
C56: 100uF; CAPMP3528X210N
C57: 100uF; SANYO-OSCON_SMD_C6
C69, C76: 100nF 100v; C0805; LCSC_PART C576517
C74: 10uF 100V; C0603; LCSC_PART C576517
C75: 2.2uF; C1206; LCSC_PART C576517
C77, C78, C79, C80, C89, C90: 10uF; C1206
C81: 100nF 100v; C0603; LCSC_PART C576517
C83: 1.5nF; C0603; LCSC_PART C576517
C84: 5.6pF; C0402; LCSC_PART C576517
C86: 220pF; C0603; LCSC_PART C576517
C113: 100nF; C0603; LCSC_PART C576517
C115: 10uF 100V; C1210; LCSC_PART C576517
C144, C145: 10uF 100V; C0805; LCSC_PART C576517
D14: SS210; DO-214AC; LCSC_PART C14996
D19: SS54; DO-214AC; LCSC_PART C14996
D20, D24: GREEN; CHIP-LED0603
D23: 1SMAF4734A; SMAF-ZDIODE
D32: RED; CHIP-LED0805
J19: DNI; 1X02
L3: 22uH; YSPI0630A-220M
L5: 68uH; DR125
L7: 150mΩ ±25% 220Ω@100MHz 0805 Ferrite Beads ROHS; FB402; LCSC_PART C139188
L8, L9, L12: 150mΩ ±25% 220Ω@100MHz 0805 Ferrite Beads ROHS; FB805; LCSC_PART C139188
P10: DB2ERC-5.08-2P-GN; MSTBA2
P23: 22284020; 1X02
P24: 1803329; PHOENIX_1803329
Q3: 2N7002-7-F; SOT-23
Q14, Q15: CSD19538Q3A
R29, R134: 2R2; R0603
R30: 180K; R0603
R38, R55, R82, R83: 10K; R0603
R43: 8K2; R0603
R56: 47k; R0603
R57: 1K91; R0603
R111, R196: 1K; R0603
R125, R132: 20K; R0603
R167: 1k5; R0603
R175: 4K7; R0603
R176: 18K; R0603
R177, R184: 5K1; R0603
R178: 620R; R0603
R179: 39K; R0603
S1: SS-12D11G5R; XKBENTERPRISESS-12D11G5R
U16: TPS54331DR; SOIC127P599X175-8N
U24: LM5146QRGYTQ1; RGY0020B
U43: EL357N-G; OPTO_EL357N-G
VR1: AMS1117-3.3

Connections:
COMP: C85.1, C86.1, U24.4 (COMP)
ESTOP_5V_EN: P23.1, P24.06
FEEDBACK24V: C83.2, C86.2, R176.1, R177.1, R178.2, U24.5 (FB)
GND: C11.2, C12.2, C13.2, C14.2, C15.2, C16.2, C17.1, C18.2, C19.1, C52.2, C53.2, C54.2, C58.2, C59.2, C69.2, C74.2, C75.2, C76.2, C77.2, C78.2, C79.2, C80.2, C84.2, C89.2, C90.2, C113.2, C115.2, C144.2, C145.2, D19.2 (A), J19.2, L9.1, P10.2, P24.01, Q15.1 (SOURCE), Q15.2 (SOURCE), Q15.3 (SOURCE), R43.2, R57.2, R82.2, R83.2, R178.1, R179.2, S1.LEFT, U16.7 (GND), U24.6 (AGND), U24.9 (NC_2), U24.12 (PGND), U24.15 (EP_2), U24.16 (NC), U24.21 (EP), U43.2 (C), VR1.1 (ADJ/GND); also elsewhere on the board
HALT_EXT: D32.C, Q3.P3 (D), R38.2; also elsewhere on the board
INPUT_VCC: C89.1, C90.1, L7.1, P10.1; also elsewhere on the board
MACRO1_EXT: P24.04; also elsewhere on the board
MACRO2_EXT: P24.03; also elsewhere on the board
MCU_GND: C55.2, C56.2, C57.-, D23.A, L9.2, Q3.P2 (S); also elsewhere on the board
MOTOR_NPGD: Q3.P1 (G); also elsewhere on the board
MOTOR_VCC_80V: R184.2; also elsewhere on the board
unnamed: D14.2 (A), L7.2
unnamed: C10.2, D19.1 (C), L3.1, U16.8 (PH)
unnamed: R29.2, U24.20 (VIN)
unnamed: C76.1, U24.3 (SS_TRK)
unnamed: R125.2, U24.8 (SYNCIN)
unnamed: R132.2, U24.10 (PGOOD)
unnamed: C75.1, R125.1, R132.1, U24.14 (VCC)
unnamed: Q14.4 (GATE), U24.18 (HO)
unnamed: C85.2, R177.2
unnamed: Q15.4 (GATE), U24.13 (LO)
unnamed: C84.1, R167.1, U24.11 (ILIM)
unnamed: R134.1, U24.17 (BST)
unnamed: C81.1, R134.2
unnamed: C81.2, L5.1, Q14.1 (SOURCE), Q14.2 (SOURCE), Q14.3 (SOURCE), Q15.5 (DRAIN), Q15.6 (DRAIN), Q15.7 (DRAIN), Q15.8 (DRAIN), Q15.9 (DRAIN), Q15.10 (DRAIN), Q15.11 (DRAIN), Q15.12 (DRAIN), R167.2, U24.19 (SW)
unnamed: C83.1, R175.1
unnamed: C18.1, U16.4 (SS)
unnamed: C10.1, U16.1 (BOOT)
unnamed: C19.2, R56.2
unnamed: D24.C, R83.1
unnamed: C17.2, R56.1, U16.6 (COMP)
unnamed: D20.C, R82.1
unnamed: L12.1, P24.07
unnamed: D32.A, R111.2
unnamed: R184.1, U43.1 (A)
unnamed: R196.2, U43.4 (CT)
POWER_IND: P24.05, U43.3 (ET)
PWR_EN: C113.1, R30.2, R43.1, S1.CENTER, U24.1 (EN_UVLO)
PWR_IN_36-80V: C69.1, C74.1, C115.1, C144.1, C145.1, D14.1 (C), Q14.5 (DRAIN), Q14.6 (DRAIN), Q14.7 (DRAIN), Q14.8 (DRAIN), Q14.9 (DRAIN), Q14.10 (DRAIN), Q14.11 (DRAIN), Q14.12 (DRAIN), R29.1, R30.1
RT: R179.1, U24.2 (RT)
START_EXT: P24.02; also elsewhere on the board
VCC_MCU_3V3: C59.1, D24.A, VR1.2 (OUT), VR1.4 (OUT); also elsewhere on the board
VCC_MCU_5V0: C54.1, C55.1, C56.1, C57.+, C58.1, D23.C, L8.1, L8.2, VR1.3 (IN); also elsewhere on the board
VCC_SYS_5V0: C11.1, C12.1, C13.1, C14.1, C52.1, C53.1, D20.A, J19.1, L3.2, L12.2, P23.2, R38.1, R55.1, R111.1; also elsewhere on the board
VCC_SYS_24V0: C15.1, C16.1, C77.1, C78.1, C79.1, C80.1, L5.2, R175.2, R176.2, R196.1, U16.2 (VIN); also elsewhere on the board
VSENSE: R55.2, R57.1, U16.5 (VSENSE)

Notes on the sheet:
Equiv to Page 19/27 of Longboard_32bit_ext_Schematic_B9_FULL_PLACE.PDF Includes Page20 of 27's 5v Power Supply Includes Page21 of 27's 24v Power Supply
DC POWER REGULATION
5V POWER SUPPLY
24V POWER SUPPLY
24.03v Output
Pin3 should be floating if unused.
POWER SWITCH
This switch will turn off all power by disabling 24V supply.
POWER LEDS
POWER HALT
POWER FILTERING AND MCU RAIL
3.3V REGULATOR
MUSHROOM BYPASS
EMERGENCY STOP

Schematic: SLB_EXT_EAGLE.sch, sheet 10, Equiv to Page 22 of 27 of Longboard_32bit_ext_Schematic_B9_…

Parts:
C87, C88: 10uF; C1206; LCSC_PART C576517
C91: 10uF 100V; C1210; LCSC_PART C576517
C92: 4.7uF; C0603; LCSC_PART C576517
C93, C104, C105, C108, C140, C142: 100nF; C0603; LCSC_PART C576517
C94: 10uF; C0603; LCSC_PART C576517
C99: 4.7uF; C0805; LCSC_PART C576517
C103: 10uF; C0805; LCSC_PART C576517
C106: 470nF; C0603; LCSC_PART C576517
C139: 4.7uF; C1206; LCSC_PART C576517
C141: 1uF; C0603; LCSC_PART C576517
C143: 22uF; C1206; LCSC_PART C576517
D36: MM3Z10VST1G; SOD-323F
D45, D47, D48: SS210; DO-214AC; LCSC_PART C14996
D46, D50: SMBJ85CA; SMBJ
D49: ZMM5V6-M; MINIMELF
D56: B5819W; SOD123FL
D57: BLUE; CHIP-LED0603
D58: RED; CHIP-LED0603
F3: 24V 460mA; 1206L
K2: VCF4-1000; TE_VCF4-1000
P6: WJ15EDGK-3.81-2P; DB2EVC-3.81-2P-GN
Q1: WSF50P10; TO252
Q13: ST3422A; SOT-23
Q16, Q17: BSS123; SOT95P240X110-3N
R42, R209, R210, R211: 0R; R0603
R70: 100R; R0603
R103, R198: 4K7; R0603
R104, R159: B57235S0100M000; B57164
R106, R162: 3K3; R0603
R126: 0.003R; R1206
R127, R212, R215: DNI; R0603
R128: 4.7R; R0603
R129: 100R; R1206
R130, R181, R197, R202: 10K; R0603
R133: 24K; R0603
R163: 100k; R0603
R173: 510K; R0603
R180, R213: 2K2; R0603
R182: DNI; R1206
R183: 100K; R0603
R199: 470K; R0603
R200, R203, R204: 1K; R0603
R201: 330K; R0603
U25: 74LVC1G08GW-Q100,1; SOT65P210X110-5N
U40: LM393DR2G; SOIC127P600X265-8N
U41: INA280A3IDCKR; DCK0005A-IPC_A
U42: SN74HC00DR; SOIC127P600X175-14N
U44: SN74LVC1G32DCKR; SOT65P210X110-5N
U50: NE555DR; SOIC-8

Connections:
5V_VCC: C104.1, C105.2, C108.2, C140.1, R106.2, R130.1, R162.2, R200.1, R201.1, U25.5 (VCC), U40.8 (VCC), U42.14 (VCC), U44.5 (VCC), U50.4 (RST), U50.8 (VCC)
24V_RELAY: D45.2 (A), F3.1, K2.86, P6.1
CTRL: C142.1, U50.5 (CTRL)
CURRENT_SENSE: C94.1, R70.2, R173.2, R210.1, R212.1
ESTOP_EN: C99.1, C103.1, D49.C, R180.1, U42.1 (1A), U42.12 (4A)
FAULT1+: R163.2, R211.2, R212.2, U40.3 (IN_A)
FAULT1-: R210.2, R215.2, U40.2 (IN_A_2)
FAULT2: R162.1, R183.1, U40.7 (OUT_B)
GND: C87.2, C88.2, C92.2, C93.2, C94.2, C99.2, C103.2, C104.2, C105.1, C106.2, C108.1, C139.2, C140.2, C142.2, C143.2, D46.A, D48.2 (A), D49.A, D50.A, Q13.P2 (S), Q17.S, R127.2, R133.2, R173.1, R180.2, R181.1, R182.1, R202.2, R203.2, R204.2, R209.2, U25.3 (GND), U40.4 (GND), U41.2 (GND), U42.7 (GND), U44.3 (GND), U50.1 (GND); also elsewhere on the board
INPUT_INRUSH: Q1.3 (D), R104.2, R126.1, U41.4 (IN+)
INPUT_VCC: C87.1, C88.1, D36.C, D50.C, Q1.2 (S), R127.1, R159.1, R197.1; also elsewhere on the board
MOTOR_NPGD: U44.4 (Y); also elsewhere on the board
MOTOR_VCC_80V: C91.2, D46.C, D48.1 (C), K2.87; also elsewhere on the board
unnamed: R104.1, R159.2
unnamed: D47.2 (A), K2.30, R126.2, R129.1, U41.5 (IN-)
unnamed: C91.1, D47.1 (C), R129.2
unnamed: Q13.P1 (G), R128.2
unnamed: F3.2, Q13.P3 (D)
unnamed: R70.1, U41.1 (OUT)
unnamed: D57.A, R213.1, U25.4 (Y)
unnamed: D57.C, R203.1
unnamed: C139.1, D56.A, R199.1, U25.2 (A)
unnamed: Q16.D, R103.2
unnamed: Q16.S, R209.1
unnamed: Q16.G, R213.2
unnamed: R181.2, U40.6 (IN_B_2)
unnamed: R183.2, U40.5 (IN_B)
unnamed: D58.C, R204.1
unnamed: R42.2, R106.1, R163.1, U40.1 (OUT_A)
unnamed: U42.2 (1B), U42.10 (3B), U42.11 (4Y)
unnamed: U42.8 (3Y), U42.13 (4B)
NTC_BYP_GATE: D36.A, Q1.1 (G), R103.1, R197.2
OCP1_THRS: R130.2, R133.1, R211.1, R215.1
OVERCURRENT_L: C106.1, R42.1, U42.9 (3A)
RELAY_ACT: C141.1, D56.C, R198.2, R199.2, U25.1 (B), U42.6 (2Y)
RELAY_GATE: Q17.D, R128.1, R182.2, R198.1
RELAY_GATE_N: U42.3 (1Y), U42.4 (2A), U42.5 (2B), U44.2 (B)
TIMER_OUT: D58.A, Q17.G, R202.1, U44.1 (A), U50.3 (OUT)
TRIG: C141.2, C143.1, R200.2, R201.2, U50.2 (TRIG), U50.7 (DIS)
VCC_SYS_5V0: C92.1, C93.1, U41.3 (VS); also elsewhere on the board
VCC_SYS_24V0: D45.1 (C), K2.85, P6.2; also elsewhere on the board

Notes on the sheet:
Equiv to Page 22/27 of Longboard_32bit_ext_Schematic_B9_FULL_PLACE.PDF
INRUSH CURRENT LIMITING
CURRENT SENSE
MAIN RELAY
CONTACTOR
Estop enable is connected from system 5V and is filtered here.
3.51V at 11.7A
Rework here for first 50 boards is to drop a 16.7K resistor onto R130, but BOM change is on R133 to 24K.
Enable Lockout should have a time constant of 10s
NTC BYPASS BUFFER
OVERCURRENT COMPARATOR
LOCKOUT TIMER
ESTOP FILTER
QUAD-NAND forms latching fault switch, reset by re-enabling etsop
LOCKOUT LATCH
LOCKOUT HALT

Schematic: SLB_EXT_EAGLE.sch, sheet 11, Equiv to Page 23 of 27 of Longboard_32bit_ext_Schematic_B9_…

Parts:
C4, C73: 100nF; C0603; LCSC_PART C576517
D2: WHITE; CHIP-LED0603
D28: RED; CHIP-LED0603
J9: 1803455; PHOENIX_1803455
J11: 1803280; PHOENIX_1803280
Q4, Q5, Q11, Q12: 2N7002-7-F; SOT-23
R24, R25, R31, R32, R35, R36, R37, R40, R41: 220R; R0402
R26, R84, R153, R154, R166, R168, R169: 10K; R0402
R34: 300R; R0402
R99: DNI; R0402
R151, R152: 4K7; R0402
R164: 4k7; R0402
R165: 510R; R0402
U3: SN74LVC2G17DBVR; SOT95P280X145-6N
U4, U5, U6, U7, U8, U10, U23: EL357N-G; OPTO_EL357N-G

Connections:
GND: C4.2, J9.05, J11.01, R26.2, U3.2 (GND), U5.3 (ET), U6.3 (ET), U23.2 (C); also elsewhere on the board
LASER_EN: Q12.P1 (G), R37.2, R166.1; also elsewhere on the board
LASER_EN_EXT: J11.03, R168.1, U8.3 (ET)
LASER_PWM: Q5.P1 (G), R41.2, R154.2; also elsewhere on the board
LASER_PWM_EXT: J11.02, U3.6 (1Y)
LASER_PWM_ISO: R169.1, U3.1 (1A), U10.3 (ET)
MCU_GND: C73.2, Q4.P2 (S), Q5.P2 (S), Q11.P2 (S), Q12.P2 (S), R84.2, R99.2, R153.1, R154.1, R166.2, R168.2, R169.2, U4.2 (C), U5.2 (C), U8.2 (C), U23.3 (ET); also elsewhere on the board
unnamed: R25.1, U4.1 (A)
unnamed: R24.2, U4.4 (CT)
unnamed: R31.1, U5.1 (A)
unnamed: R165.1, U23.1 (A)
unnamed: R32.1, U6.1 (A)
unnamed: R34.2, U7.4 (CT)
unnamed: D2.A, R151.1
unnamed: R35.1, U7.1 (A)
unnamed: D2.C, Q4.P3 (D)
unnamed: D28.A, R152.1
unnamed: D28.C, Q5.P3 (D)
unnamed: R41.1, U10.1 (A)
unnamed: Q12.P3 (D), R99.1, U10.2 (C)
unnamed: R37.1, U8.1 (A)
unnamed: R36.2, U8.4 (CT)
unnamed: R40.2, U10.4 (CT)
SPINDLE_CONN: J9.04, U3.4 (2Y)
SPINDLE_DIR: R31.2; also elsewhere on the board
SPINDLE_EN: Q11.P1 (G), R84.1; also elsewhere on the board
SPINDLE_EN_5V: U7.3 (ET); also elsewhere on the board
SPINDLE_PWM: Q4.P1 (G), R25.2, R153.2; also elsewhere on the board
SPINDLE_PWM_ISO: R26.1, U3.3 (2A), U4.3 (ET)
SPIN_AT_SPEED: J9.01, R165.2
SPIN_DIR_12V: J9.03, U5.4 (CT)
SPIN_EN: Q11.P3 (D), U6.2 (C), U7.2 (C)
SPIN_EN_12V: J9.02, U6.4 (CT)
SPIN_SPEED: C73.1, R164.1, U23.4 (CT); also elsewhere on the board
VCC_MCU_3V3: R32.2, R35.2, R164.2; also elsewhere on the board
VCC_MCU_5V0: R34.1, R151.2, R152.2; also elsewhere on the board
VCC_SYS_5V0: C4.1, R24.1, R36.1, R40.1, U3.5 (VCC); also elsewhere on the board

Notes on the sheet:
Equiv to Page 23/27 of Longboard_32bit_ext_Schematic_B9_FULL_PLACE.PDF
Spindle
Laser
U3_1
ON EXPANSION HEADER

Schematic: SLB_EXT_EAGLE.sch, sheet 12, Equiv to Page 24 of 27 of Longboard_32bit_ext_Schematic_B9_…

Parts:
C60: 4.7uF; C0603
C61: 22uF; C0603; LCSC_PART C576517
C62, C63, C65, C66: 100nF; C0603; LCSC_PART C576517
C64: 1uF; C0603; LCSC_PART C576517
D25: RED; CHIP-LED0603
D26: GREEN; CHIP-LED0603
D41: ZMM5V6-M; LL-34
D42: ZMM3V3-M; LL-34
J14: KH-PCB-6P6C
L10, L11: 150mΩ ±25% 220Ω@100MHz 0805 Ferrite Beads ROHS; FB805; LCSC_PART C139188
R85, R88: 200R; R0402
R86: 47K; R0402
R87: 120R; R0402
R90, R91, R92, R93, R94, R95: 2K; R0402
U18: CBMUD1201LAS8; SOIC-8
U19: PCA82C250T/YM; SO8
U21, U22: EL357N-G; OPTO_EL357N-G

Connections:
CANH: J14.2, R87.2, U19.7 (CANH)
CANL: J14.3, R87.1, U19.6 (CANL)
CAN_RX: R94.1, U18.2 (VOA); also elsewhere on the board
CAN_TX: R95.1, U18.3 (VIB); also elsewhere on the board
GND: C60.2, L11.1; also elsewhere on the board
HALT_PEN: J14.4, U21.2 (C)
HALT_PENDANT: C65.1, R90.1, U21.4 (CT); also elsewhere on the board
KPSTR: C66.1, R92.1, U22.4 (CT); also elsewhere on the board
KPSTR_PEN: J14.5, U22.2 (C)
MCU_GND: C62.2, C65.2, C66.2, D42.A (+), U18.4 (GND1), U21.3 (ET), U22.3 (ET); also elsewhere on the board
unnamed: D25.C, R94.2
unnamed: D26.C, R95.2
unnamed: C62.1, R85.1, U18.1 (VDD1)
unnamed: U18.7 (VIA), U19.4 (RXD)
unnamed: U18.6 (VOB), U19.1 (TXD)
unnamed: C63.2, R88.1, U18.8 (VDD2)
unnamed: R86.2, U19.8 (RS)
unnamed: R91.1, U21.1 (A)
unnamed: R93.1, U22.1 (A)
PENDANT_VCC_5V0: C61.1, C64.1, D41.C (-), J14.1, L10.2, R88.2, R91.2, R93.2, U19.3 (VCC)
PEND_GND: C61.2, C63.1, C64.2, D41.A (+), J14.6, L11.2, R86.1, U18.5 (GND2), U19.2 (GND); also elsewhere on the board
VCC_MCU_3V3: D25.A, D26.A, D42.C (-), R85.2, R90.2, R92.2; also elsewhere on the board
VCC_MCU_5V0: C60.1, L10.1; also elsewhere on the board

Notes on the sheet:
Equiv to Page 24/27 of Longboard_32bit_ext_Schematic_B9_FULL_PLACE.PDF
CANBUS PENDANT
KPSTR = KEYPAD STROBE In grblHAL its now called I2C Strobe: Works with https://github.com/grblHAL/Plugin_keypad

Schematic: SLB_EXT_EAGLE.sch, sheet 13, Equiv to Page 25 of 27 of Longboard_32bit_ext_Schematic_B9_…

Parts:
D27: USBLC6-2SC6; SOT95P280X145-6N
J20: USB-C-Socket; USB-C-16P
L13: DLW21HN900SQ2L; FIL_DLW21HN900SQ2L
R107, R108: 4K7; R0402

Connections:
CONN_USB_D_N: D27.3 (I/O2_IN), D27.4 (I/O2_OUT), J20.A7 (D-), J20.B7 (D-), L13.1
CONN_USB_D_P: D27.1 (I/O1_IN), D27.6 (I/O1_OUT), J20.A6 (D+), J20.B6 (D+), L13.4
MCU_GND: D27.2 (GND), J20.GND, J20.GND2 (GND), J20.SHLD1 (SHLD), J20.SHLD2 (SHLD), J20.SHLD3 (SHLD), J20.SHLD4 (SHLD), J20.SHLD5 (SHLD), J20.SHLD6 (SHLD), J20.SHLD7 (SHLD), J20.SHLD8 (SHLD), R107.1, R108.1; also elsewhere on the board
USBC_CC1: J20.A5 (CC1), R108.2
USBC_CC2: J20.B5 (CC2), R107.2
USB_D_N: L13.2; also elsewhere on the board
USB_D_P: L13.3; also elsewhere on the board
VBUS: D27.5 (VBUS), J20.VBUS1 (VBUS), J20.VBUS2 (VBUS)

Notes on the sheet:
Equiv to Page 25/27 of Longboard_32bit_ext_Schematic_B9_FULL_PLACE.PDF
USB

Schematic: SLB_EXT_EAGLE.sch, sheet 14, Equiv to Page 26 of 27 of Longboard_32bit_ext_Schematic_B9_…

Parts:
C7: 4.7uF; C0603
C8: 22uF; C0603; LCSC_PART C576517
C9: 1uF; C0603; LCSC_PART C576517
C134, C135: 100nF; C0603; LCSC_PART C576517
D1: ZMM3V3-M; LL-34
D16: SM712; SOT23
D17: RED; CHIP-LED0603
D18: GREEN; CHIP-LED0603
D40: ZMM5V6-M; LL-34
J10: DB2EVC-3.81-4P-GN
J12: KH-PCB-6P6C
L1, L2: 150mΩ ±25% 220Ω@100MHz 0805 Ferrite Beads ROHS; FB805; LCSC_PART C139188
R44, R45, R50: 200R; R0402
R46, R48: 560R; R0402
R47, R52, R53, R54: 2K; R0402
R49: 130R; R0402
R51: 220R; R0402
U12: CBMUD1201LAS8; SOIC-8
U13: SN75176BDR; SOIC127P599X175-8N
U15: EL357N-G; OPTO_EL357N-G

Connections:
A: D16.2 (Z2), J10.03, J12.4, R48.1, R49.2, U13.6 (A)
B: D16.1 (Z1), J10.04, J12.3, R46.2, R49.1, U13.7 (B)
DI: R50.2, U12.6 (VOB)
GND: C7.2, L2.1; also elsewhere on the board
MCU_GND: C134.2, D1.A (+), U12.4 (GND1), U15.2 (C); also elsewhere on the board
MOD_GND: C8.2, C9.1, D16.3 (COM), D40.A (+), J10.01, J12.1, J12.6, L2.2, R46.1, R52.2, U12.5 (GND2), U13.5 (GND)
unnamed: C134.1, R44.1, U12.1 (VDD1)
unnamed: C135.2, R45.1, U12.8 (VDD2)
unnamed: R50.1, U13.4 (D)
unnamed: R51.1, U15.1 (A)
unnamed: D17.C, R53.2
unnamed: D18.C, R54.2
PEND_GND: C135.1; also elsewhere on the board
RE: R52.1, U13.2 (!RE), U13.3 (DE), U15.3 (ET)
RO: R47.1, U12.7 (VIA), U13.1 (R)
RS485_DIR: R51.2; also elsewhere on the board
RXD_RS485: R53.1, U12.2 (VOA); also elsewhere on the board
TXD_RS485: R54.1, U12.3 (VIB); also elsewhere on the board
VCC_MCU_3V3: D1.C (-), D17.A, D18.A, R44.2; also elsewhere on the board
VCC_SYS_5V0: C7.1, L1.1; also elsewhere on the board
VCC_SYS_5V0_RS485: C8.1, C9.2, D40.C (-), J10.02, L1.2, R45.2, R47.2, R48.2, U13.8 (VCC), U15.4 (CT)

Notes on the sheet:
Equiv to Page 26/27 of Longboard_32bit_ext_Schematic_B9_FULL_PLACE.PDF
RS-485

Board: 2 copper layers, 706 parts (0 on the bottom side), 421 nets, no tracks yet.

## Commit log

2024-02-14 Initial commit of original SLB files to be modified.
    [12V_Power_Supply.SchDoc, 3V3_Digital_Out.SchDoc, 5V_Digital_Out.SchDoc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]
2024-02-16 Commit some updates around the MOSFET selection and overall DC power section.
    [24V_Power_Supply.SchDoc, 5V_Power_Supply.SchDoc, DC_Power_Regulation.SchDoc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]
2024-02-20 Commit current WIP power supply.
    [24V_Power_Supply.SchDoc, DC_Power_Regulation.SchDoc, Longboard_32bit_ext.PrjPCB]
2024-02-20 Commit WIP LM5069
    [24V_Power_Supply.SchDoc, DC_Power_Regulation.SchDoc]
2024-02-28 Commit current WIP.
    [24V_Power_Supply.SchDoc, 5V_Digital_Out.SchDoc, 5V_Power_Supply.SchDoc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]
2024-03-06 Commit current WIP
    [24V_Power_Supply.SchDoc, 5V_Power_Supply.SchDoc, DC_Power_Regulation.SchDoc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]
2024-03-13 Commit initial complete placement.
    [24V_Power_Supply.SchDoc, DC_Power_Regulation.SchDoc, Limit_Switches.SchDoc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]
2024-04-01 BOM updates WIP
    [24V_Power_Supply.SchDoc, 3V3_Digital_Out.SchDoc, 5V_Digital_Out.SchDoc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]
2024-04-02 Update parts for availability
    [24V_Power_Supply.SchDoc, 3V3_Digital_Out.SchDoc, 5V_Digital_Out.SchDoc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]
2024-04-03 Filled in more component parameters
    [24V_Power_Supply.SchDoc, 5V_Power_Supply.SchDoc, DC_Power_Regulation.SchDoc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]
2024-04-03 Swapping in parts for availability
    [Longboard_32bit_ext.PrjPCB, Neopixel_Driver.SchDoc, Stepper_driver_group.SchDoc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]
2024-04-03 Added fuses and extra power connector.
    [DC_Power_Switching.SchDoc, Longboard_32bit_ext.PrjPCB, Relay_Driver.SchDoc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]
2024-04-08 Commit current CAM
    [24V_Power_Supply.SchDoc, 3V3_Digital_Out.SchDoc, 5V_Digital_Out.SchDoc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]
2024-06-09 Commit B9 updates.
    [Change Log.SchDoc, DC_Power_Switching.SchDoc, JLPCB BOM-Longboard_32bit_ext_B9_FULL_PLACE.xlsx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]
2024-06-09 Commit project files.
    [Longboard_32bit_ext.PrjPCB]
2025-11-12 Added AutoDesk EAGLE Schematic
    [SLB_EXT_EAGLE.brd, SLB_EXT_EAGLE.sch]
2025-11-12 Updated schematic
    [SLB_EXT_EAGLE.brd, SLB_EXT_EAGLE.sch]
2025-11-12 Updated schematic (Incorrectly named NET)
    [SLB_EXT_EAGLE.brd, SLB_EXT_EAGLE.sch]
2025-11-27 Fix disconnected nets on BAT54S components
    [SLB_EXT_EAGLE.brd, SLB_EXT_EAGLE.sch]

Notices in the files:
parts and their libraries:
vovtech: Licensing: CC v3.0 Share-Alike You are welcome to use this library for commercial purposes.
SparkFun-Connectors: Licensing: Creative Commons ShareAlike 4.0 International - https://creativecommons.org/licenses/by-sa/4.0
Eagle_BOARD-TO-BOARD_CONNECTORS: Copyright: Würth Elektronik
